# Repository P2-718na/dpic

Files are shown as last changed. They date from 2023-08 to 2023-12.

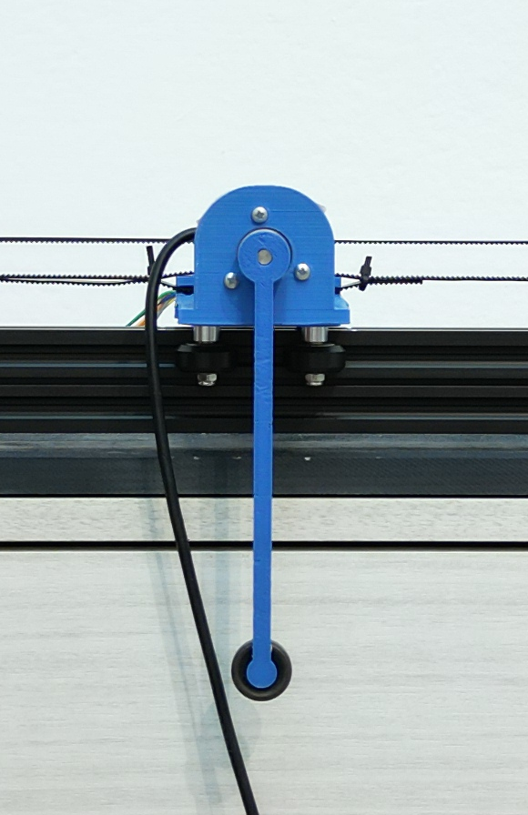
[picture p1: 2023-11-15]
docs/report/assets/dettaglio-carrello.png

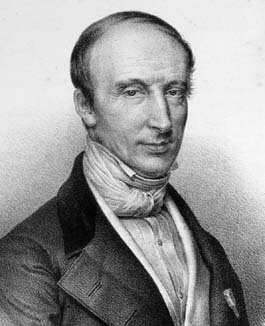
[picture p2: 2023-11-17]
docs/report/assets/cauchy.png

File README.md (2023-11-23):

# inverted-pendulum
tbd

## Repository structure
- 📁 [code](https://github.com/P2-718na/dpic/tree/master/code)
  - Code used for pendulum control and data acquisition.
- 📁 [docs](https://github.com/P2-718na/dpic/tree/master/docs)
  - Final report and other documentation.
- 📁 [scripts](https://github.com/P2-718na/dpic/tree/master/scripts)
  - npm scripts.

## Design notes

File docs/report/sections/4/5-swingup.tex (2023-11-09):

\section{Strategia di swing-up}
Per lo swing-up uso il metodo di Ljapunov.
%così come descritto in [Astrom Furuta swinging up a pendulum by energy control].
%todo ref
Ricavo l'energia del solo pendolo e la uso per cercare una funzione
di controllo di Ljapunov.

\subsection{Energia del pendolo}
\label{subsec:energia-pendolo}
L'energia del solo pendolo è data da
\begin{align*}
    E &= T + V\\
      &= \frac 1 2 I \dot \theta^2 + mgl(\cos\theta-1)
    \numberthis \label{eq:energia-pendolo}
\end{align*}
dove ho scelto il potenziale in modo che si annulli quando $\theta=0$. Voglio studiare che effetto ha un accelerazione del perno sul pendolo. Risolvo l'equazione di eulero:
\begin{equation*}
    \totald t \partiald {\dot \theta} {\mathcal L} - \partiald {\theta} {\mathcal L} = -lma \cos \theta
\end{equation*}
dove $\mathcal L$ è la Lagrangiana del solo pendolo e a secondo membro compare il momento torcente che l'accelerazione $a$ imprime al pendolo.
Ottengo
\begin{equation}
    I \ddot \theta - mgl\sin \theta + mal \cos \theta = 0
    \label{eq:moto-pendolo}
\end{equation}
%todo qui bisogna sistemare un po' i simboli
e posso usare le due equazioni \eqref{eq:moto-pendolo} e \eqref{eq:energia-pendolo} per calcolare la variazione di energia istantanea che produce l'accelerazione $a$ lungo la traiettoria del moto.
Ottengo
\begin{equation*}
    \begin{aligned}
        \frac{dE}{dt}
        &= \totald t \left(\frac 1 2 I \dot \theta ^2 + mgl \cos \theta  \right) \\
        &= I \dot \theta \ddot \theta - mgl \sin \theta \cdot \dot \theta \\
        &= -mal \cos \theta \cdot \dot \theta
        .
        \label{eq:effetto-energia}
    \end{aligned}
\end{equation*}

\subsection{Funzione di controllo di Ljapunov}
Cerco una funzione di controllo di Ljapunov.
Prendo
\begin{equation}
    V = V(\b x) = \frac 1 2 E^2
        \label{eq:lyapunov-energy}
\end{equation}
e cerco una strategia di controllo $a$ per cui
\begin{equation*}
    \frac{dV}{dt}(\b x) < 0 \text{ con } \b x \neq \b 0,
\end{equation*}
secondo la proposizione~\ref{prop:condizione-sufficiente-ljapunov}.
Calcolo la derivata
\begin{align*}
    \frac{dV}{dt} &= \totald t \left( \frac 1 2 \dot E^2\right) \\
    &=  E \dot E \\
    &=  E (-mal \dot \theta \cos \theta) \numberthis\label{eq:dvdt}.
\end{align*}
La scelta più semplice è definire $a$ come funzione a tratti:
\begin{equation*}
    a = \left\{
    \begin{aligned}
         &a_{\max}\sign{\dot \theta \cos \theta} &\text{ se } E < 0 \\
         -&a_{\max}\sign{\dot \theta \cos \theta} &\text{ se } E > 0 \\
         &0 &\text{ altrimenti}
    \end{aligned}
    \right.
\end{equation*}
con $a_{\max}$ l'accelerazione massima possibile per il sistema.
La figura~\ref{fig:energy-control} mostra che questa strategia porta il sistema a
zero.

\begin{figure}
    \centering
    \begin{subfigure}[b]{0.48\textwidth}
        \centering
        
        \caption{aaaaa}
    \end{subfigure}
    \hfill
    \begin{subfigure}[b]{0.48\textwidth}
        \centering
        
        \caption{bbbbb}
    \end{subfigure}
    \caption{Schema del sistema.} %todo
    \label{fig:energy-control}
\end{figure}

La funzione segno nella~\eqref{eq:bang-bang} la rende difficile da studiare
ed estremamente sensibile al rumore (la minima oscillazione costringe il motore
a passare istantaneamente da potenza zero a potenza massima).
Considero l'alternativa
\begin{equation}
    a = a_{\max} \tanh(E \dot \theta \cos \theta).
    \label{eq:control-strategy-tanh}
\end{equation}

Dimostro che la~\eqref{eq:lyapunov-energy} con $a$ definito come
nella~\eqref{eq:control-strategy-tanh} è una funzione di controllo di Ljapunov.

Uso la~\eqref{eq:dvdt}:
\begin{align*}
    \frac{dV}{dt} &=  E (-mal \dot \theta \cos \theta)\\
    &= -Eml \dot \theta \cos \theta \cdot a_{\max} \tanh(E \dot \theta \cos \theta). \numberthis\label{eq:a-ljapunov}
\end{align*}
ed è immediato verificare che la~\eqref{eq:a-ljapunov} è sempre negativa.
La~\eqref{eq:control-strategy-tanh} è rappresentata in figura~\ref{fig:energy-control-better}.

\begin{figure}[b]
    \centering
    \begin{subfigure}[b]{0.48\textwidth}
        \centering
        
        \caption{aaaaa}
    \end{subfigure}
    \hfill
    \begin{subfigure}[b]{0.48\textwidth}
        \centering
        
        \caption{bbbbb}
    \end{subfigure}
    \caption{Schema del sistema.} %todo
    \label{fig:energy-control-better}
\end{figure}

Concludo osservando che la strategia che ho mostrato in questo paragrafo
non tiene conto della posizione del carrello sulla rotaia.
È quindi necessario passare alla strategia di stabilizzazione
una volta che il pendolo ha raggiunto la verticale.

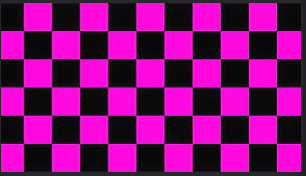
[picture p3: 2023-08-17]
docs/report/assets/missing.png

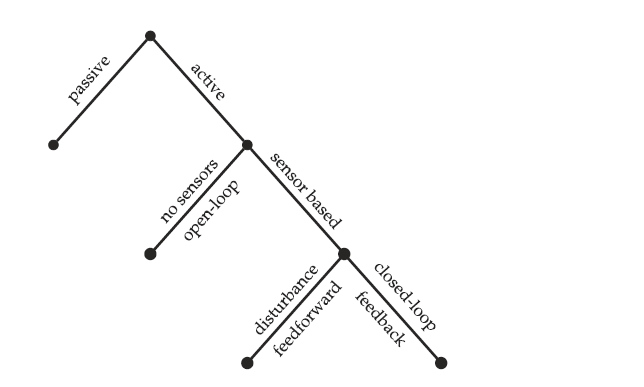
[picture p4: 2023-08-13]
docs/report/assets/control-types.png

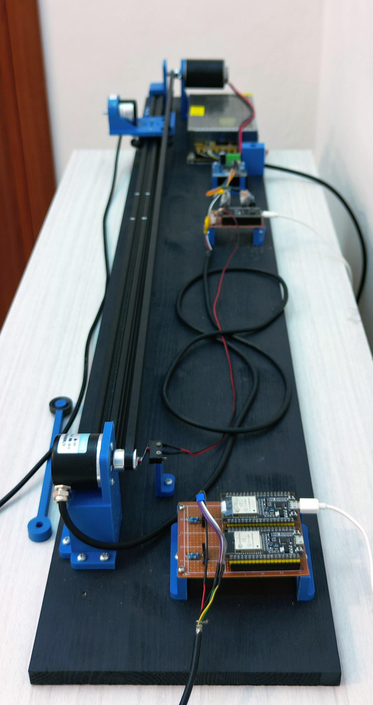
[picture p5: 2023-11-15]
docs/report/assets/lato.png

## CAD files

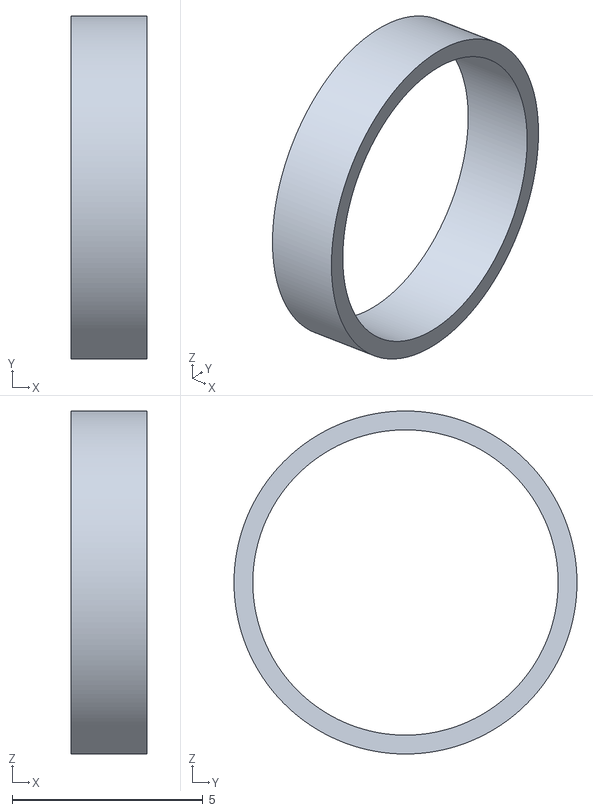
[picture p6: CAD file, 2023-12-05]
stl/spacer bearing.stl
2.00 x 8.99 x 8.99

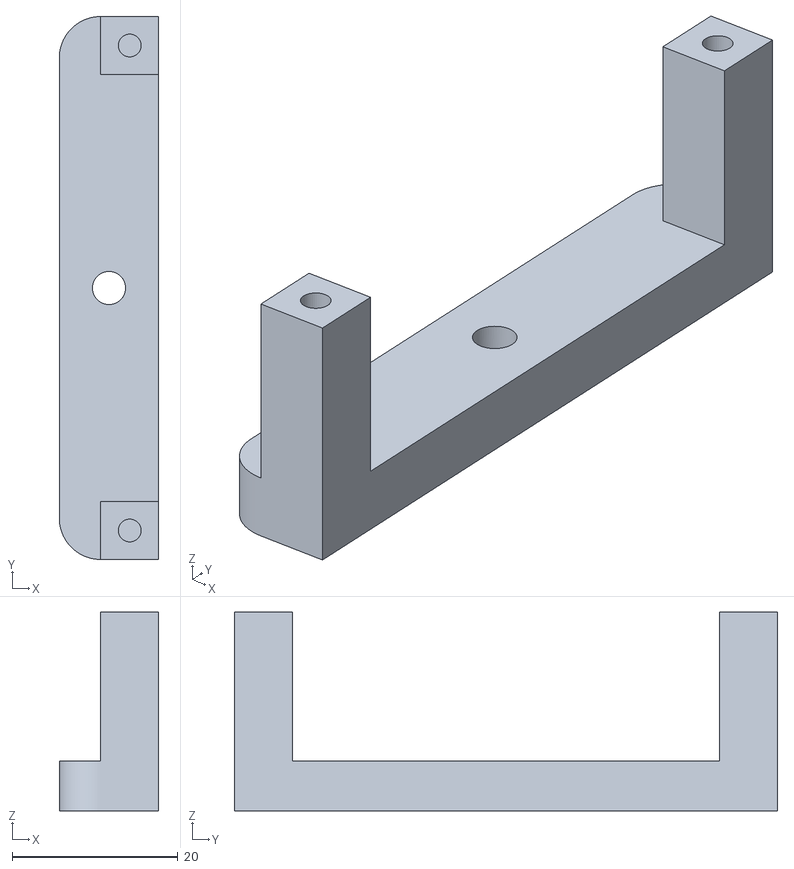
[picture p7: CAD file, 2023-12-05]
stl/raiser2.stl
12.0 x 65.5 x 24.0

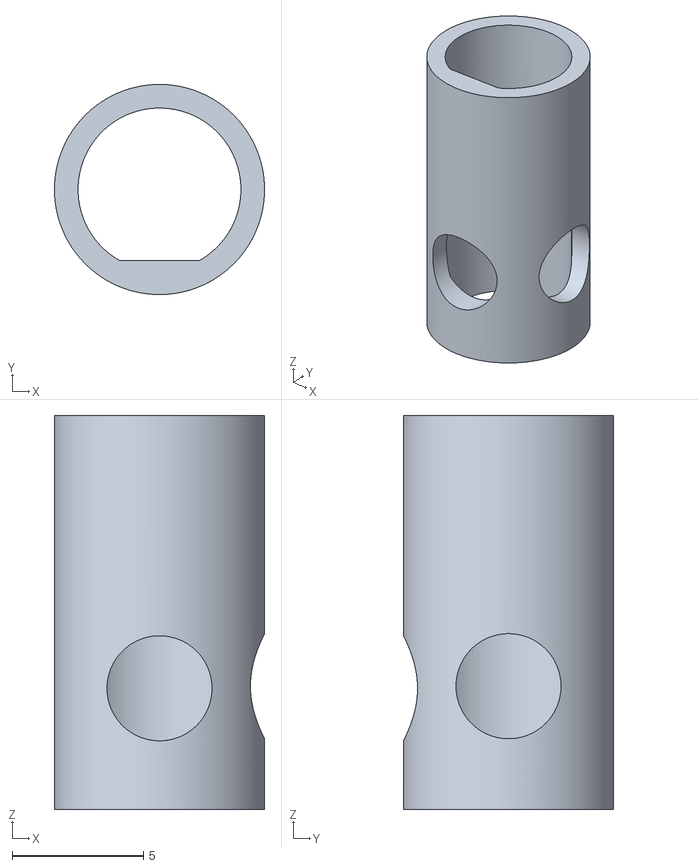
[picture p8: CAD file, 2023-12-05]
stl/Corpo67.stl
8.00 x 8.00 x 15.0

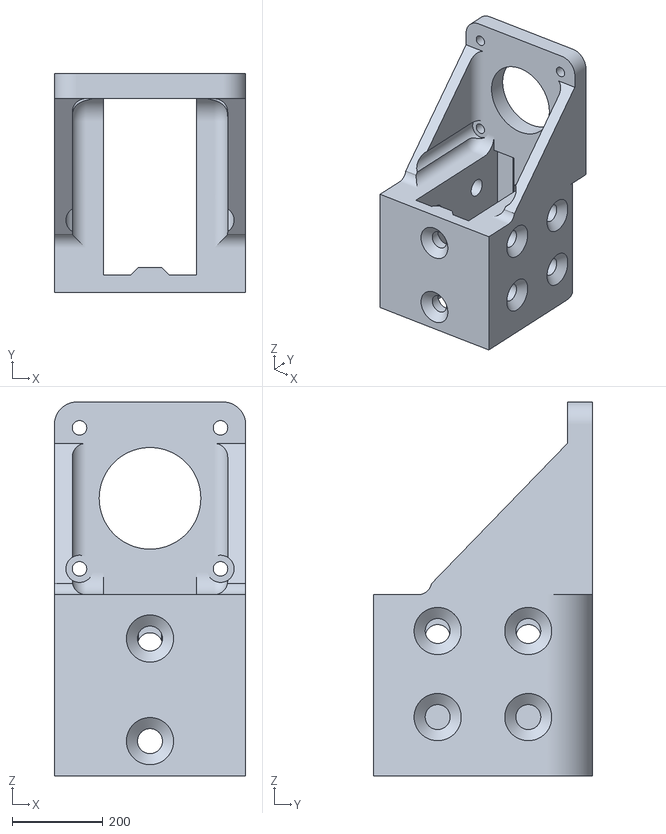
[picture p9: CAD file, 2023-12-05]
stl/holder.stl
422.2 x 482.4 x 825.0

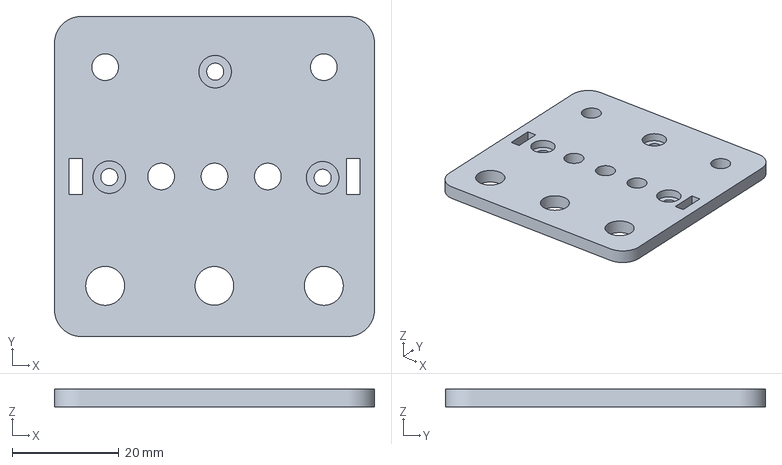
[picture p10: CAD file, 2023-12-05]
stl/GANTRY ADAPTER.3mf
60.0 x 60.0 x 3.35 mm

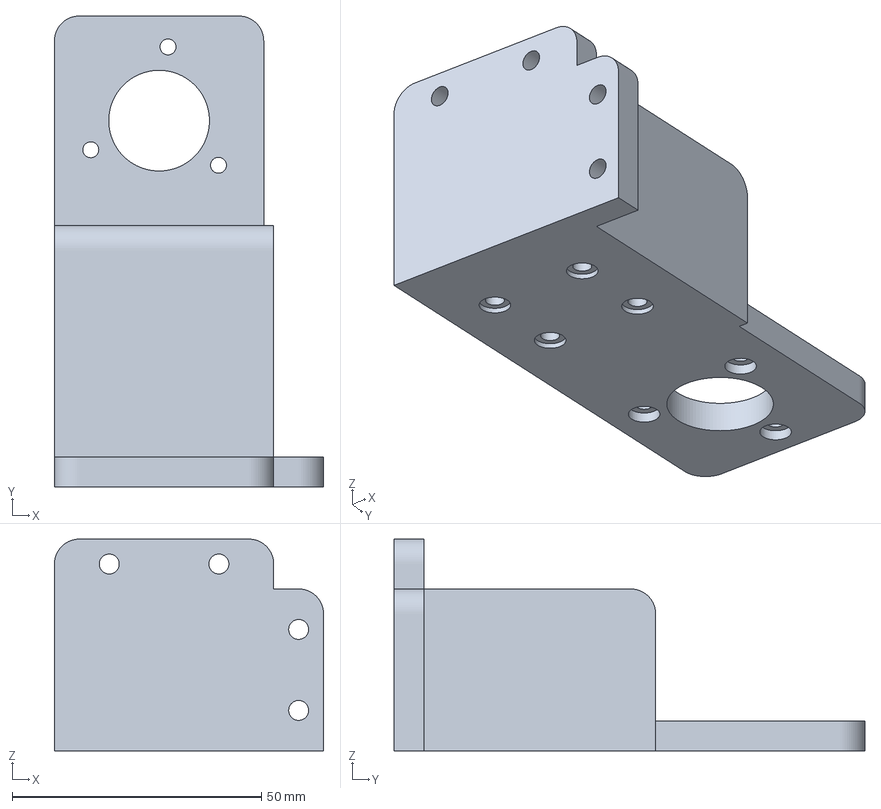
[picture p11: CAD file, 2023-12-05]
stl/stepper holder.3mf
54.0 x 94.5 x 42.5 mm

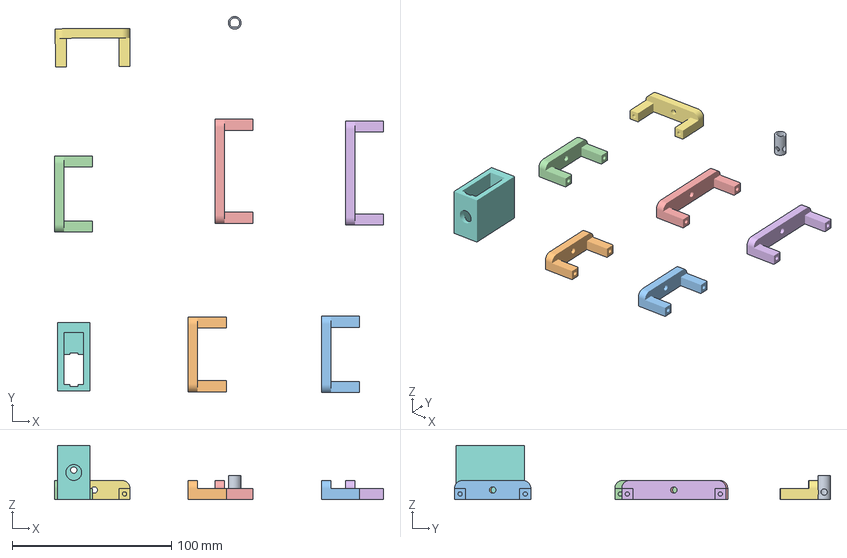
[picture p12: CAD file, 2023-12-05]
stl/last bits.3mf
207.2 x 236.4 x 34.0 mm
Corpo67.stl
raiser4.stl x 2
raiser3.stl x 2
raiser2.stl x 2
button.stl

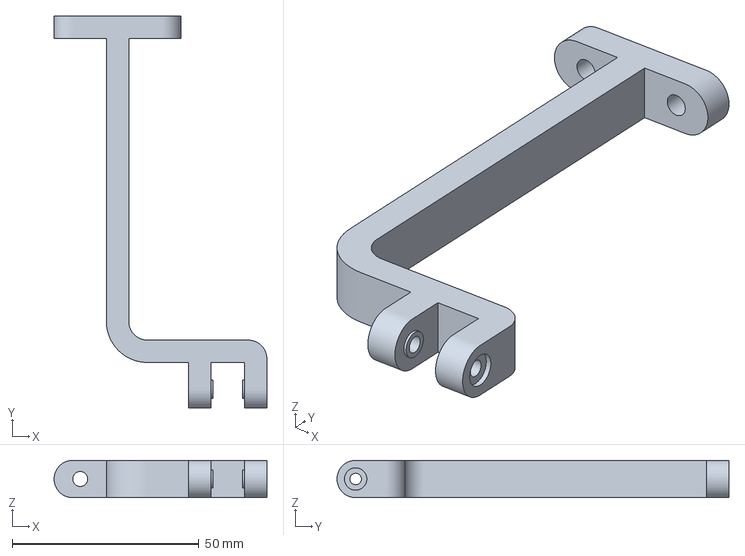
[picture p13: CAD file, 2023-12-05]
stl/tensioner.3mf
57.0 x 105.0 x 10.0 mm

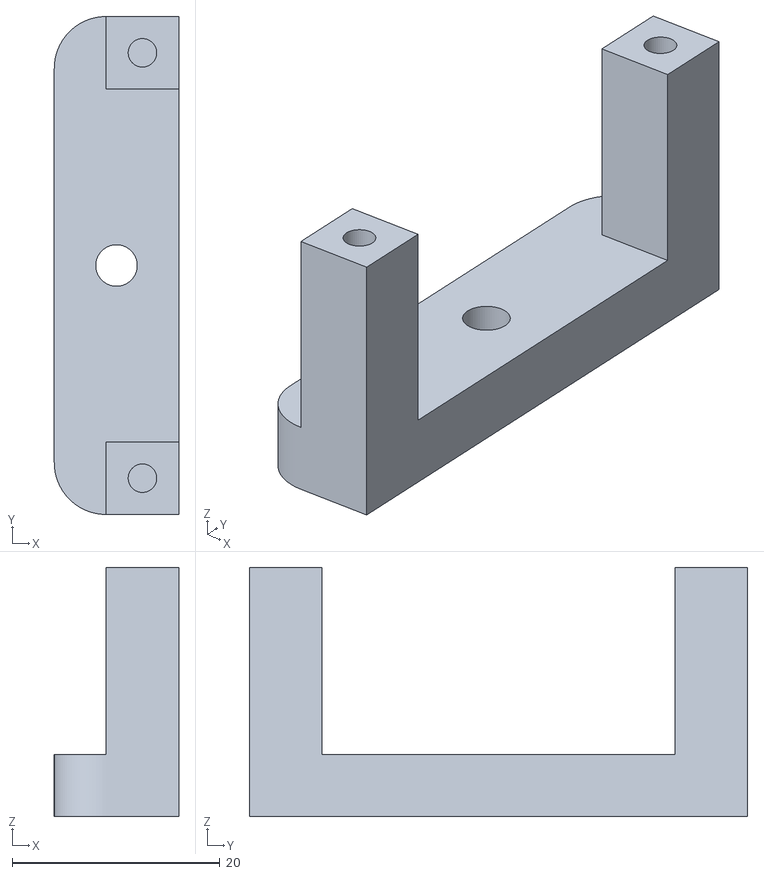
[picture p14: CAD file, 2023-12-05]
stl/raiser3.stl
12.0 x 48.0 x 24.0

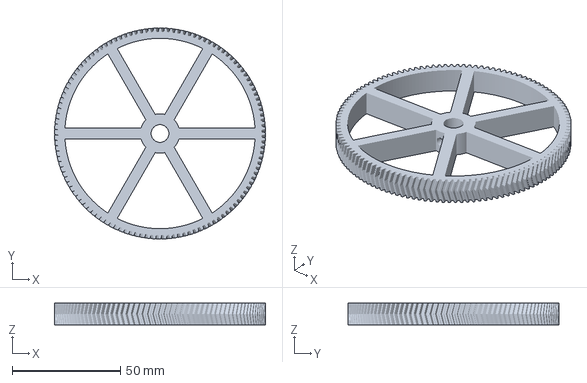
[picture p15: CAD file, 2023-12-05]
stl/gear.3mf
97.6 x 97.6 x 10.0 mm

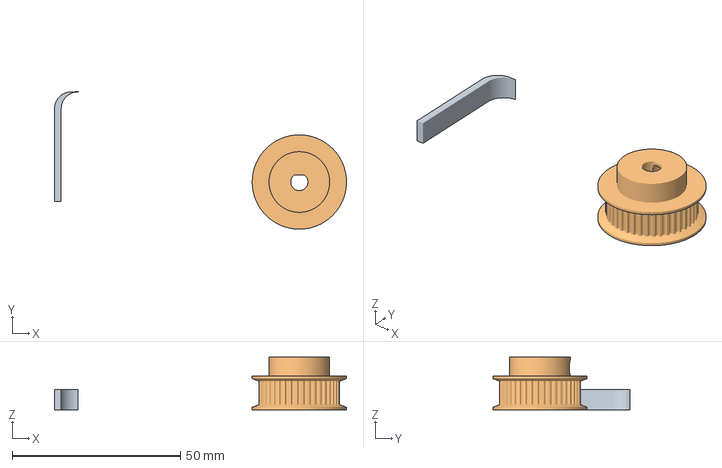
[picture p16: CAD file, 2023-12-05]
stl/pulley 40teeth.3mf
86.7 x 40.8 x 15.6 mm
Corpo148.stl
pulley 40teeth.stl

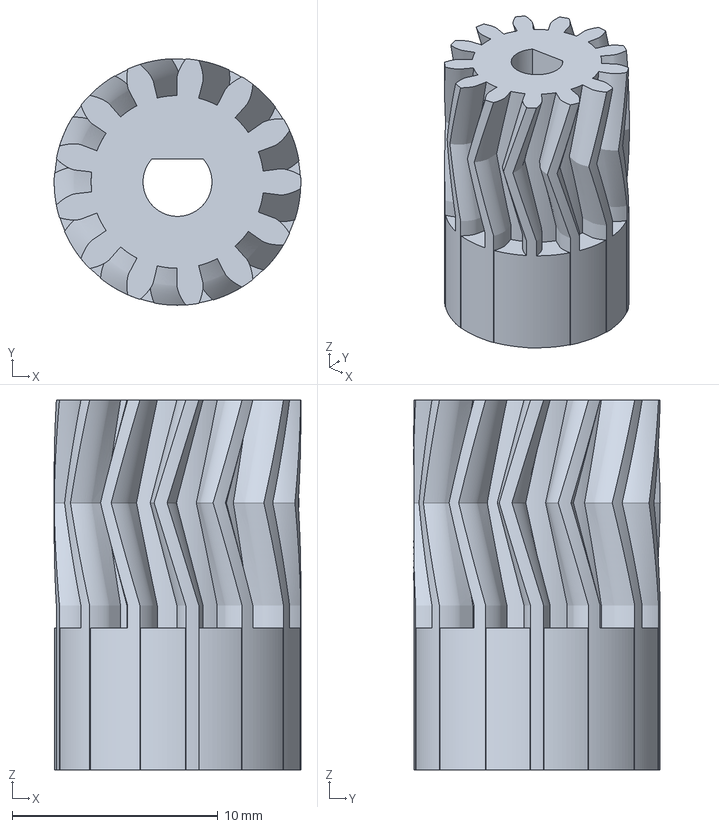
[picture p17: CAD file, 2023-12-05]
stl/gear small.3mf
12.0 x 12.0 x 18.0 mm

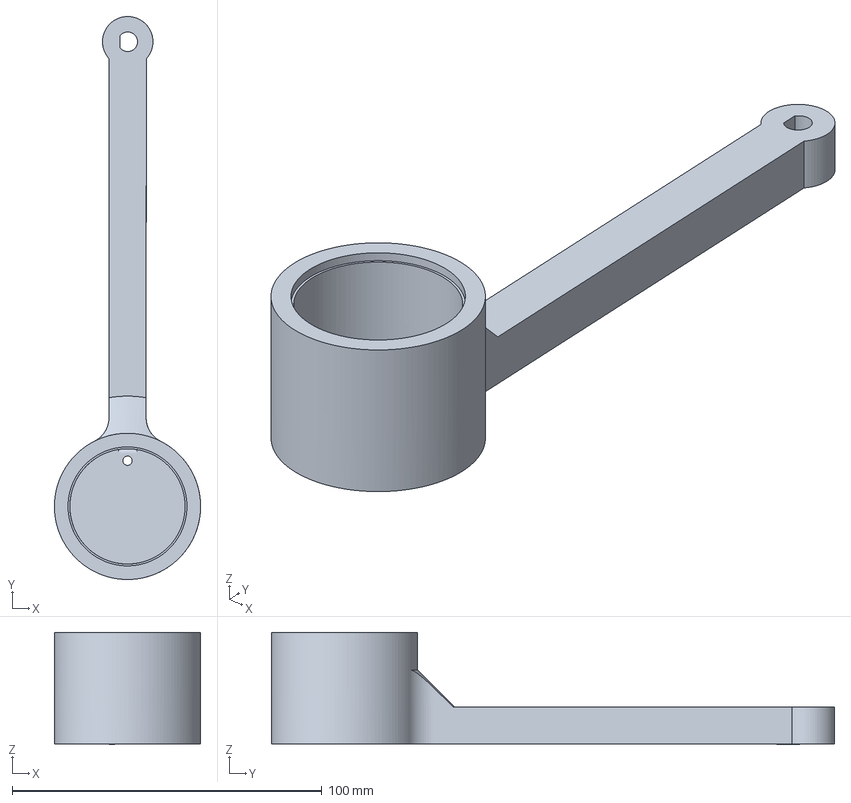
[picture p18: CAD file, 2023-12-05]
stl/Corpo1.3mf
47.2 x 181.7 x 36.2 mm

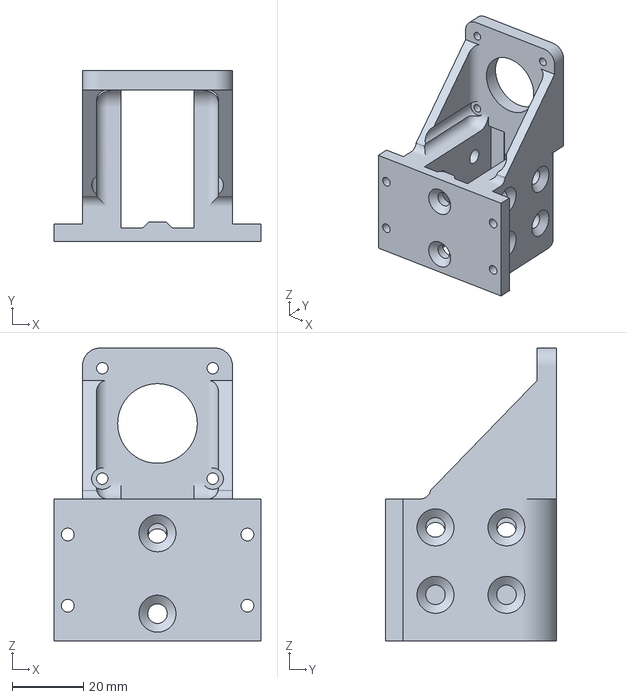
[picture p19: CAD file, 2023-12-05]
stl/Corpo della mesh1.3mf
58.2 x 48.2 x 82.5 mm

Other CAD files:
stl/rod2.3mf
stl/gears.3mf
stl/Corpo79.stl
stl/raiser4.stl
stl/Corpo1.stl
stl/Extrusion.f3d
stl/arm2.3mf
stl/button.stl
stl/encoder pulley.3mf
stl/lato Corpo1.3mf
stl/mover.f3d
stl/pulley 40teeth.stl
stl/stabilizer.stl
stl/tensioner.stl

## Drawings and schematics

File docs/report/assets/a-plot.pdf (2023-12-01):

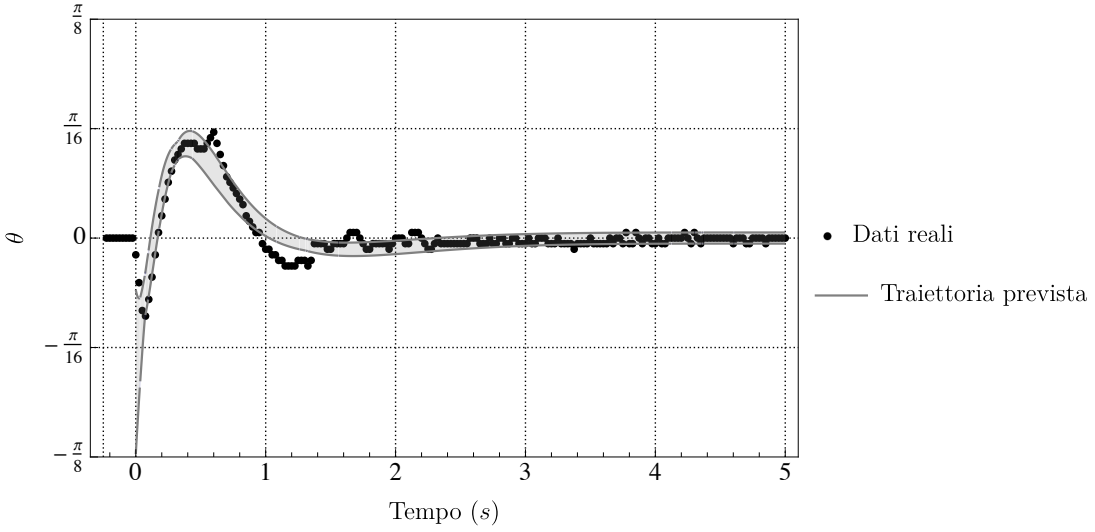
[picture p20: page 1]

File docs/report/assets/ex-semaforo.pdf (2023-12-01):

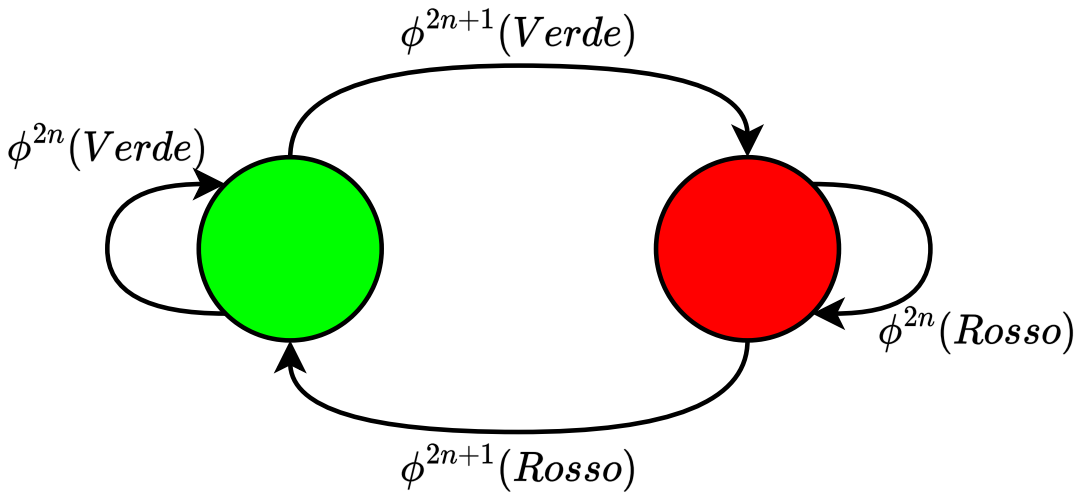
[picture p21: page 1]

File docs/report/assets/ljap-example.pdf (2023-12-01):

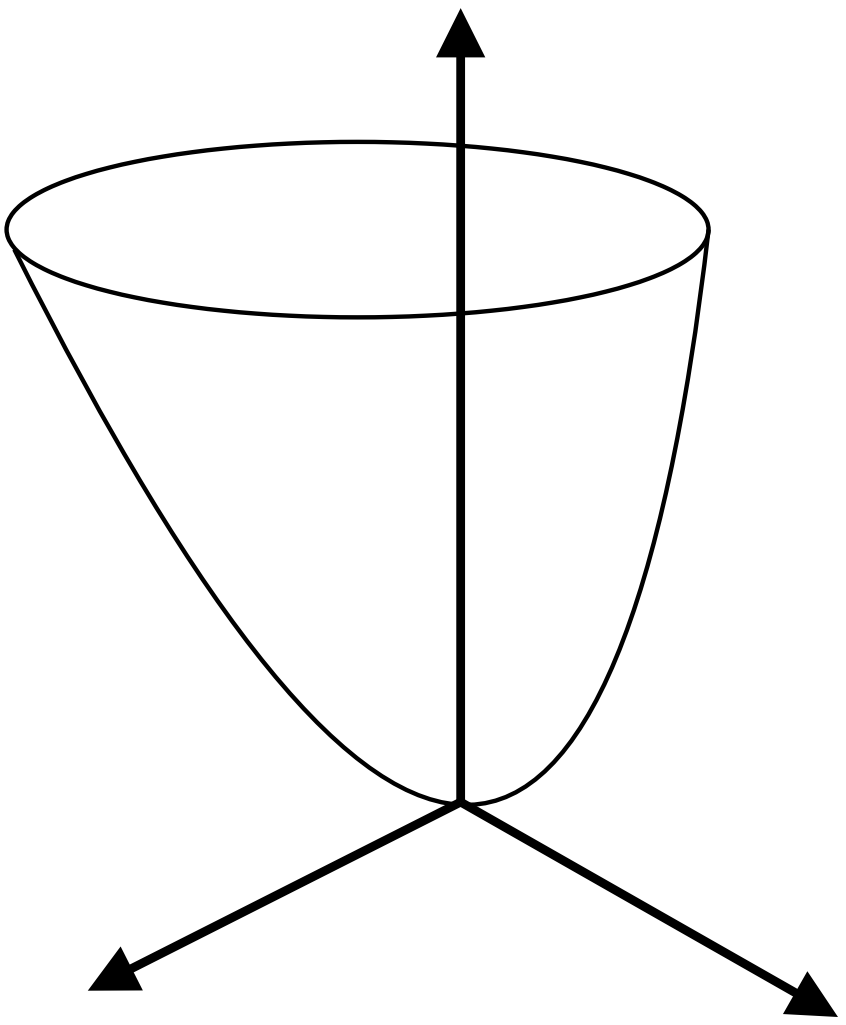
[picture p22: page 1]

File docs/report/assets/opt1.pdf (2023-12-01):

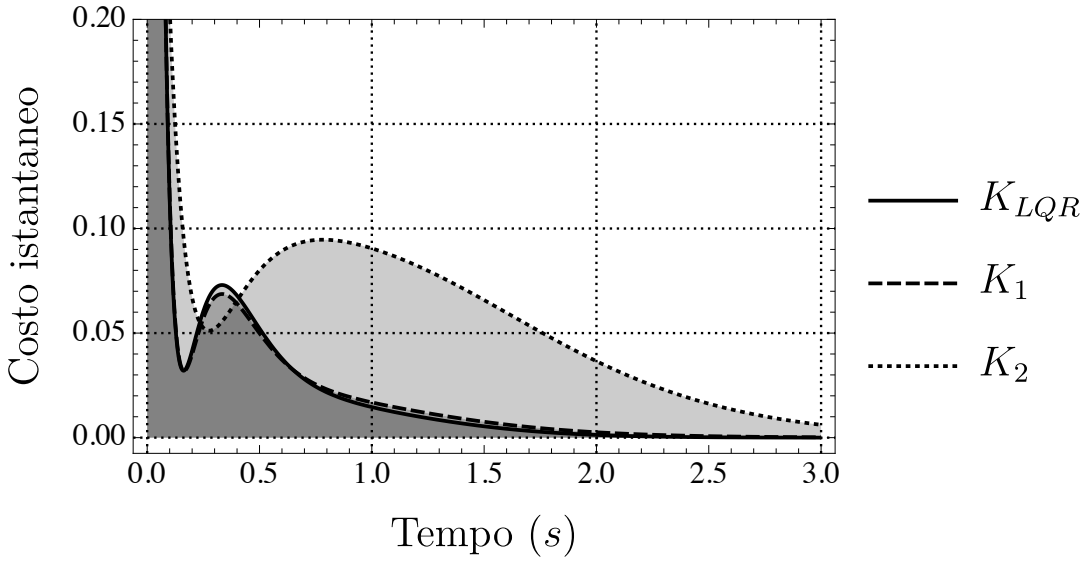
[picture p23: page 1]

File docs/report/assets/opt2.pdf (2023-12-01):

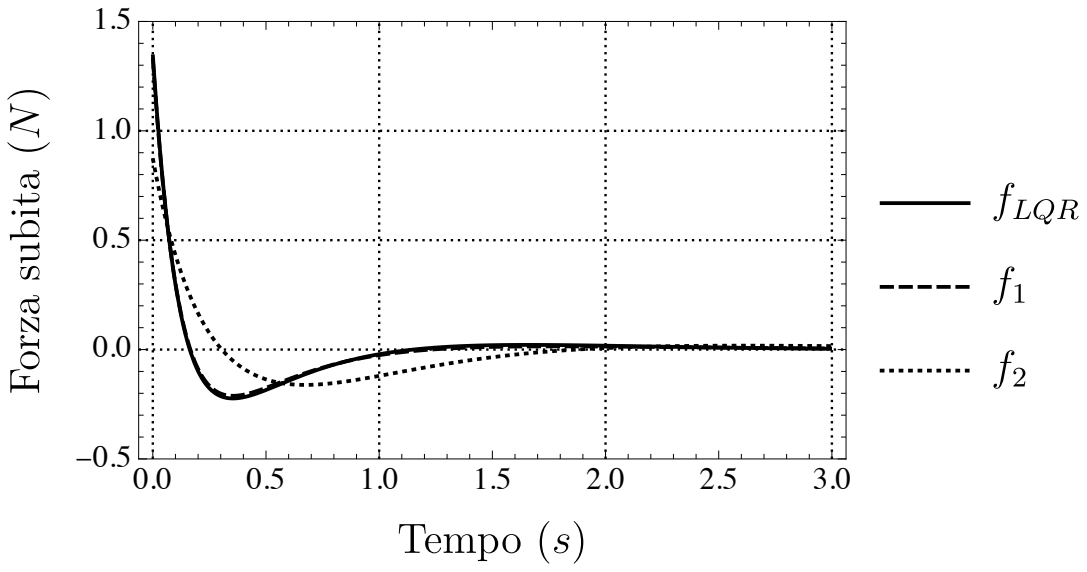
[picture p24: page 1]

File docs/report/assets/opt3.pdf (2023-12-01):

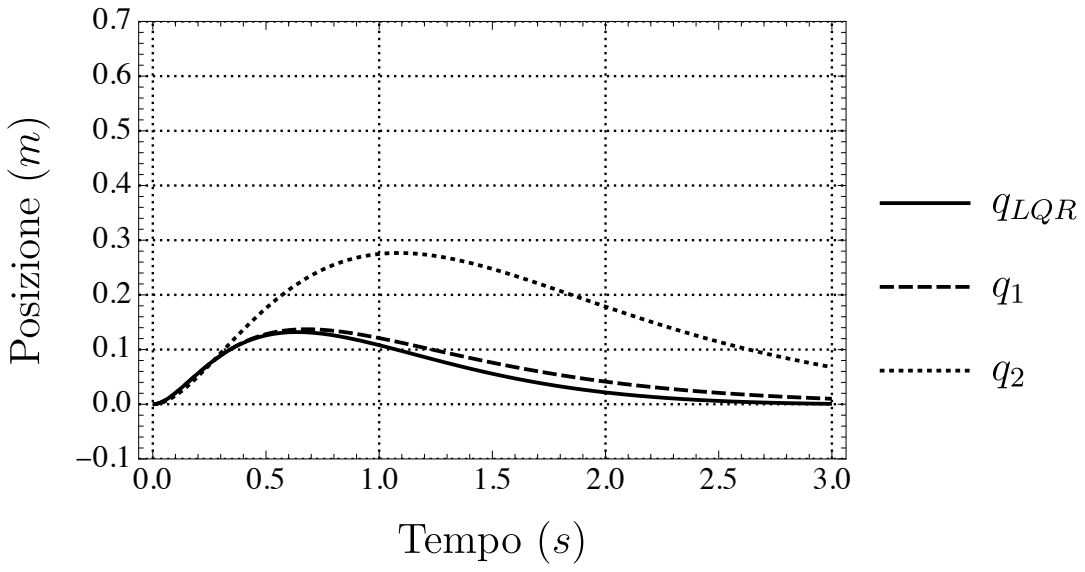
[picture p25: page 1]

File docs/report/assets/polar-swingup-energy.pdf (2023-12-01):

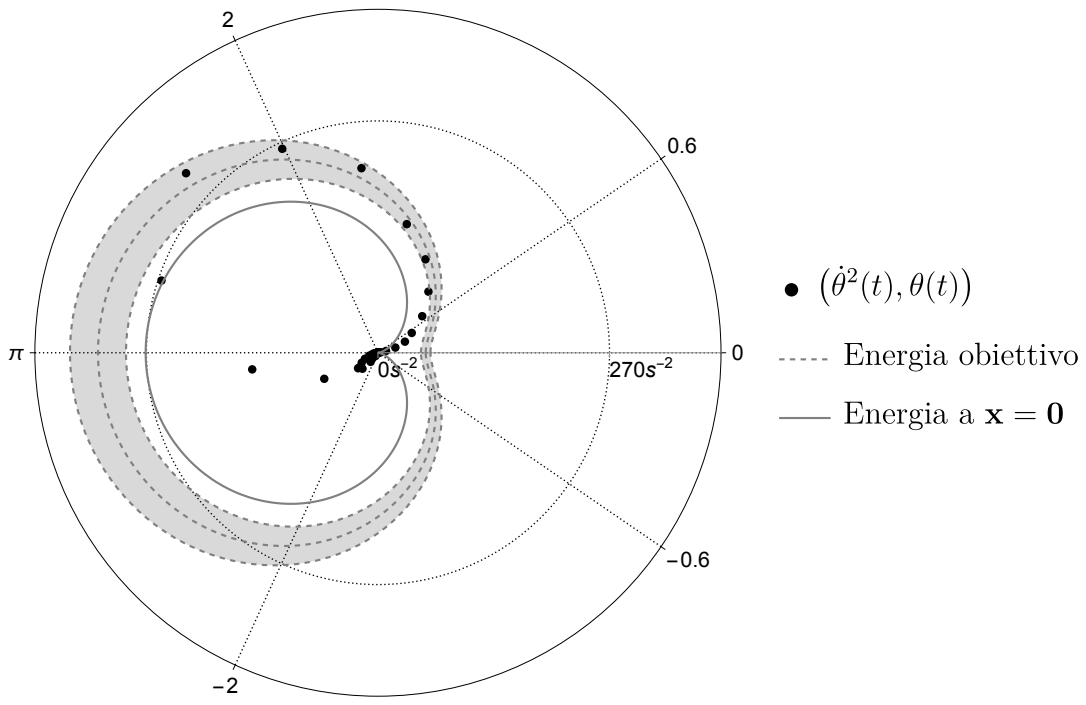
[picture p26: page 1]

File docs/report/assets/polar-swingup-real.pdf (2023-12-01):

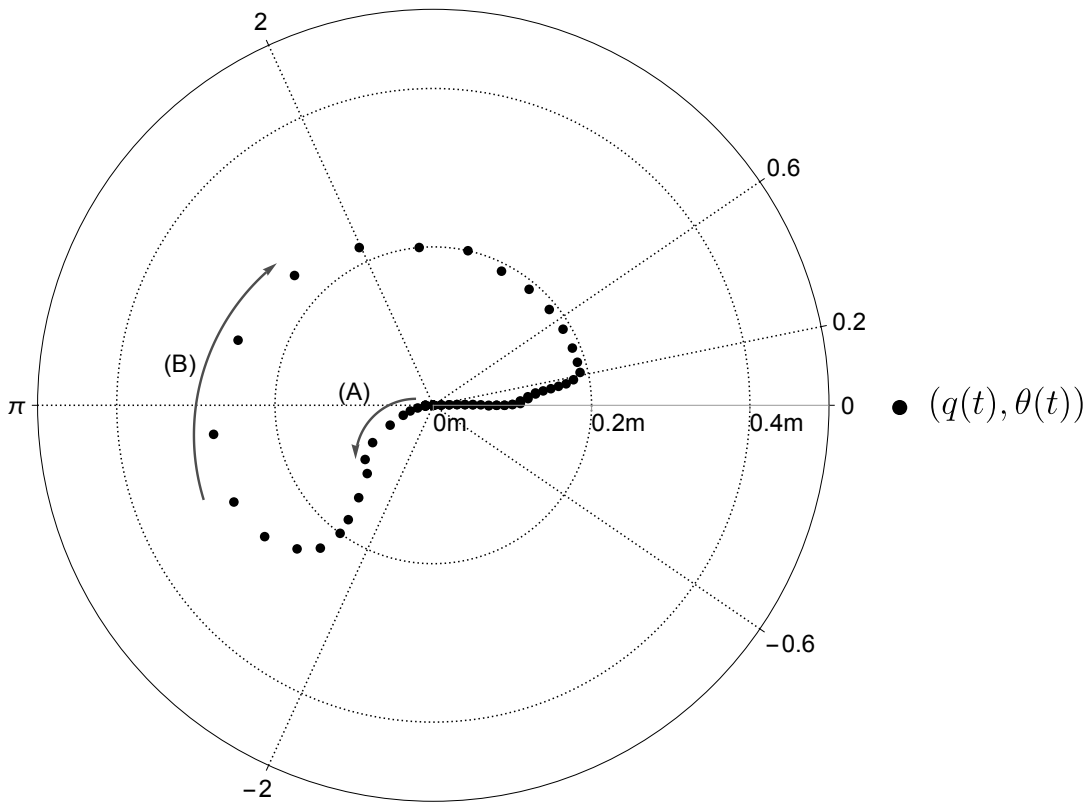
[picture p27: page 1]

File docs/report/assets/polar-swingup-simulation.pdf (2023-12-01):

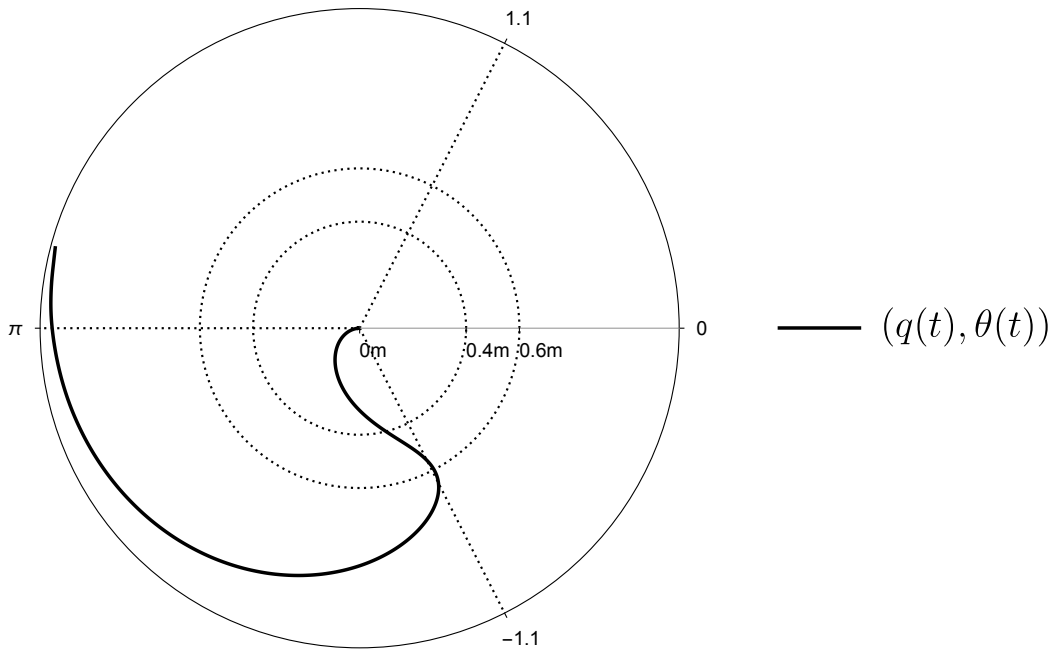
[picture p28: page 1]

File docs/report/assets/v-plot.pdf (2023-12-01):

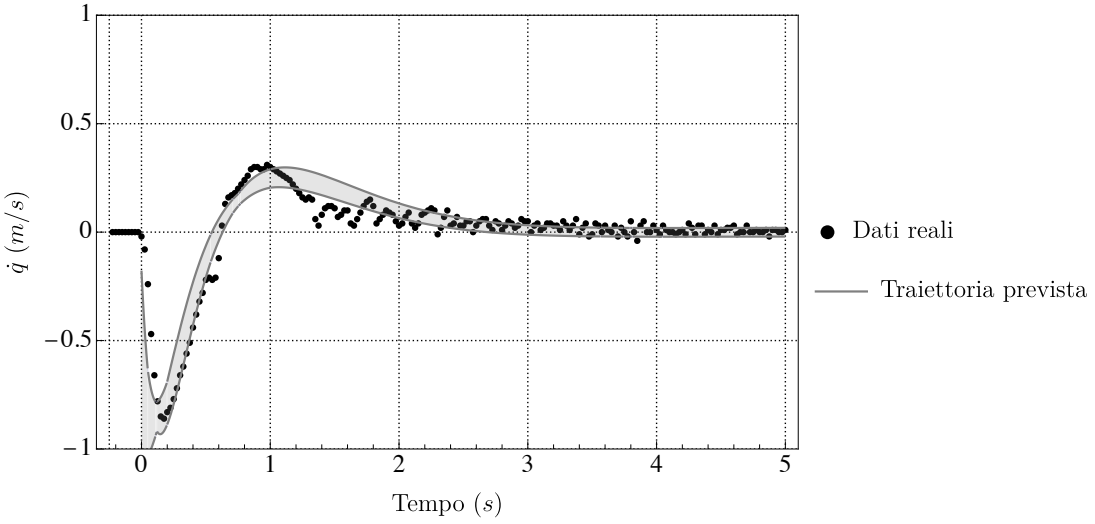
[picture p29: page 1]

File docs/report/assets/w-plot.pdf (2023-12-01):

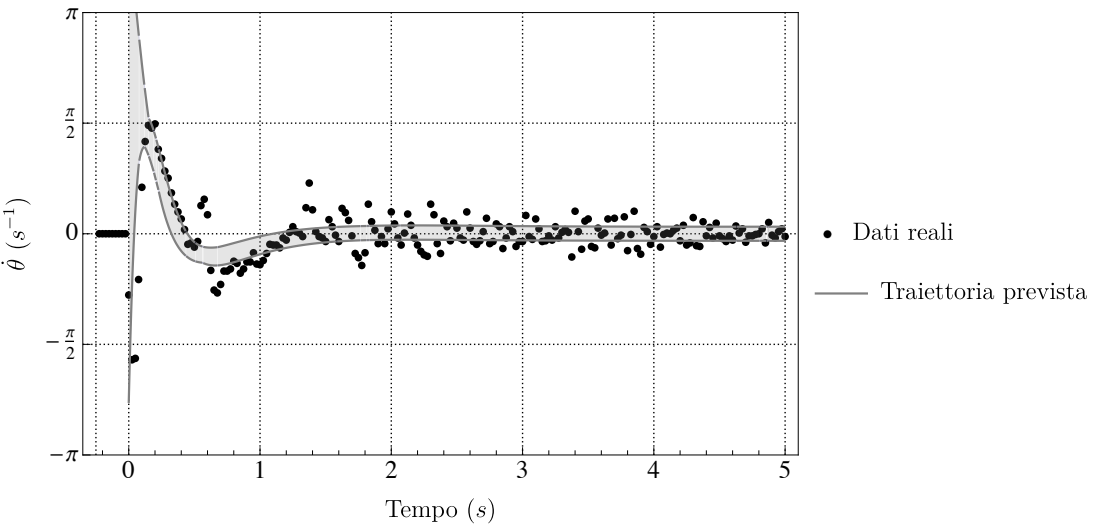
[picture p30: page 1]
πππ2

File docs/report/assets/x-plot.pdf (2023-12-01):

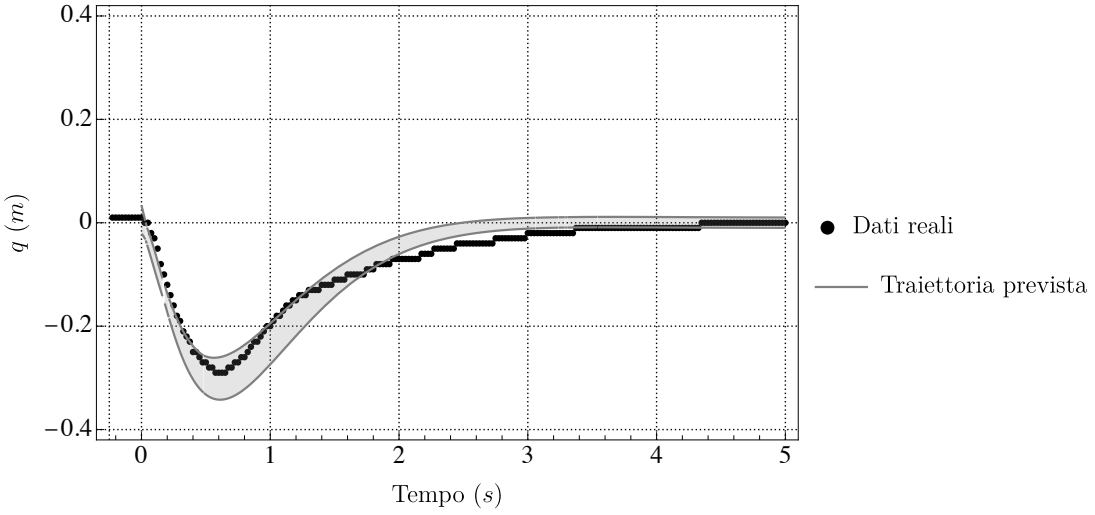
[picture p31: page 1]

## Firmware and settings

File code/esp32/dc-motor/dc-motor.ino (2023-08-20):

#include <esp_now.h>
#include <WiFi.h>
#include <Encoder.h>


// Constants 
#define RPWM_OUT 32
#define LPWM_OUT 33
#define RPWM_CHANNEL 0
#define LPWM_CHANNEL 1

#define ENCODER_A 35
#define ENCODER_B 34


// State  and control /////////////////////////////////////////////
struct State {
  float x, v, a1, w1, a2, w2;

  float optimalControl() {
    //return 2*cos(millis()/200.);
    return 1;
  }

  bool controllable() {
    return x < .7  && x > .01;
  }
};
State state;
void printState();


// Second core and x, v encoder ///////////////////////
volatile int steps;
void loop2(void * params) {
  Encoder encoder(ENCODER_A, ENCODER_B); //todo possibly edit code to add esp32 attribute needed for interrupts

  int lastStep = steps % 2400;
  for (;;) {
    steps = encoder.read();
  }
}

void setup2() {
  TaskHandle_t core2;

  xTaskCreatePinnedToCore(
      loop2, /* Function to implement the task */
      "DAQ", /* Name of the task */
      10000,  /* Stack size in words */
      NULL,  /* Task input parameter */
      0,  /* Priority of the task */
      &core2,  /* Task handle. */
      0); /* Core where the task should run */ //?? 
}



// First core //////////////////////////////////////////
void setup() {
  // Setup second core
  setup2();

  // Setup motor
  // channel, freq, resolution(bits)
  ledcSetup(RPWM_CHANNEL, 500, 8);
  ledcSetup(LPWM_CHANNEL, 500, 8);
  ledcAttachPin(RPWM_OUT, RPWM_CHANNEL);
  ledcAttachPin(LPWM_OUT, LPWM_CHANNEL);

  // Initialize communications
  Serial.begin(115200);
}

void loop() {

  // todo make better
  static int lastMicros;
  static int lastSteps;
  static int deltaTime;

  deltaTime = micros() - lastMicros;
  if (deltaTime > 5000) {
    constexpr float toMeters = .853 / 51144.;

    state.x = steps * toMeters;
    state.v = ((steps - lastSteps) * 1E6) / deltaTime * toMeters;
    lastMicros = micros();
    lastSteps = steps;
  }

  printState(state);

  applyControl(state);
}



// Function definitions /////////////////////////////////////
void printState(State& state) {
  static bool init = false;
  if (!init) {
    Serial.println("x v a1 w1 a2 w2");

    init = true;
  }

  static int interval = millis();
  if (millis() - interval < 100) {
    return;
  }

  Serial.print(state.x);
  Serial.print(" ");
  Serial.print(state.v);
  Serial.print(" ");
  Serial.println();

  interval = millis();
}

void applyControl(State& state) {
  static int interval = millis();
  if (millis() - interval < 20) {
    return;
  }


  float control = state.optimalControl();

  // QUi ci andrà uno switch per tutti i possibili stati del sistema (down, up, swing up...)
  if (state.controllable()) {
    //Serial.print("+");
    driveMotorWithForce(control, state.v);
    return;
  }

  //Serial.print("=");
  driveMotorWithForce(0, 0);
}

template <typename T> int sgn(T val) {
    return (T(0) < val) - (val < T(0));
}

// PEso motore: 225g senza filo, 240g con filo.
void driveMotorWithForce(float f, float v) {
    constexpr float A =  .656;
    constexpr float B =  .0616;
    constexpr float C = -.0535;

    // deltaT
    constexpr float dT = .02;

    //m
    constexpr float m = .8;

    float u = 
      ((1 - A)*v + dT*f/m - C*sgn(v))
      / 
      B;
    u = u *255./12.;

    if (f == 0) {
      ledcWrite(LPWM_CHANNEL, 0);
      ledcWrite(RPWM_CHANNEL, 0);

      return;
    }

    ledcWrite(LPWM_CHANNEL, (int)(u > 0 ?  u : 0));
    ledcWrite(RPWM_CHANNEL, (int)(u < 0 ? -u : 0));
}

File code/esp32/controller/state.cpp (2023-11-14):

#include "state.h"
#include "math.h"

State::State() : printInterval(Interval(25)), controlInterval(Interval(5)), currentControl(0) {}

void State::init() {
  Serial.println("x v a1 w1 a2 w2");
}

float State::optimalControl() {
 // return 1;
 // SIngle pendulum
  return (6.63*x + 6.77*v + 12.89*a1 + 1.5*w1);
  return -(1.8*x + 2.9*v - 30*a1 - 0.97*w1 + 80.5*a2 + 8.00*w2)*.1;
}

bool State::controllable() {
  //return x <.6 && x >.01;
  return (a1 > -.6  && a1 < .6 && x < .35 && x > -.35 && abs(w1) < 6 && abs(v) < 2);
  return (a1 > -.8  && a1 < .8 && x < .35 && x > -.35 && a2 > -.5  && a2 < .5);
}

void State::updateControl() {
  // Qui ci va lo switch in base allo stato del sistema...
  if (!controllable()) {
    currentControl = 0;

    constexpr float aMax = 18;
    const float E = .0243628 * (cos(a1) - 1) + .00018 * w1*w1;

    const float ctrl = aMax * tanh(
        (E -.010) * w1 * cos(a1)
    );

    if (abs(a1) > 2 && x < .3 && x > -.3) {
      currentControl = ctrl;
    }

    return;
  }

  //Serial.print(millis());
  //Serial.println("+");
  currentControl = optimalControl();
}

int State::convertToPWM(float force) {
  constexpr float A = 28.5;
  constexpr float B = 120 ; // Dovrebbe essere 8, ma 8 non va lol

  float u = A*force + B*v;

  return u;
}

void State::updateMotor() {
  if (currentControl == 0) {
    ledcWrite(LPWM_CHANNEL, 0);
    ledcWrite(RPWM_CHANNEL, 0);

    return;
  }

  int u = convertToPWM(currentControl);

  constexpr int LPWM_MIN = 33; //32 safe
  constexpr int RPWM_MIN = 33; // 32 safe

  ledcWrite(LPWM_CHANNEL, (int)(u > 0 ?  (u < LPWM_MIN ? u + LPWM_MIN : u): 0));
  ledcWrite(RPWM_CHANNEL, (int)(u < 0 ?  (-u < RPWM_MIN ? -u + RPWM_MIN : -u) : 0));
}

void State::print() {
  Serial.print("( ");
  Serial.print(x*10);
  Serial.print(", ");
  Serial.print(v*10);
  Serial.print(", ");
  Serial.print(a1*10);
  Serial.print(", ");
  Serial.print(w1*10);
  Serial.print(", ");
  Serial.print(a2);
  Serial.print(", ");
  Serial.print(w2);
  Serial.print(", ");
  Serial.print(optimalControl());
  Serial.print(", ");
  Serial.print(convertToPWM(optimalControl()));
  Serial.print(", ");
  Serial.print((int)controllable());
  Serial.print(" )");
  Serial.println();
}

void State::loop() {
  if (printInterval.ready()) {
    print();
    printInterval.reset();
  }

  updateMotor();

  if (controlInterval.ready()) {
    updateControl();
    controlInterval.reset();
  }
}

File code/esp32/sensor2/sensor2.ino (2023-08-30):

#include <esp_now.h>
#include <WiFi.h>
#include <Encoder.h>
#include <Ewma.h>
//EwmaT <int> speedFilter(33, 100);

#define ENCODER_A 35
#define ENCODER_B 34
#define BROADCAST_ADDRESS {0xBC, 0xDD, 0xC2, 0xD4, 0x52, 0x28}

struct Variable {
  byte id;
  float q;
  float q_dot;
};
Variable data;
uint8_t broadcastAddress[] = BROADCAST_ADDRESS;
void setupEspNow();



volatile int steps;
int euclideanMod(int a, int b);
void loop2(void * params) {
  Encoder encoder(ENCODER_A, ENCODER_B); //todo possibly edit code to add esp32 attribute needed for interrupts

  for (;;) {
    // maybe I cann add some sort of timer here...
    steps = encoder.read();
  }
}

void setup2() {
  TaskHandle_t core2;

  xTaskCreatePinnedToCore(
      loop2, /* Function to implement the task */
      "DAQ", /* Name of the task */
      10000,  /* Stack size in words */
      NULL,  /* Task input parameter */
      0,  /* Priority of the task */
      &core2,  /* Task handle. */
      0); /* Core where the task should run */ //??
}



void setup() {
  // Setup second core
  setup2();
  // For some reason, initializing serial here and not writing to console breaks esp now... ?
  //Serial.begin(115200);

  setupEspNow();
}

void loop() {
  static int lastMicros = 0;
  static int deltaTime;
  static int lastSteps;
  deltaTime = micros() - lastMicros;

  //if (deltaTime1 > 1001) {
  //  speedFilter.filter((steps - lastSteps) * 1E6 / deltaTime1);
  //  lastSteps = steps;
  //  lastMicros1 = micros();
  //}

  // 5ms delay between sends
  if (deltaTime > 2000) {
    constexpr float toRadians = M_PI / 1200.;

    // Just to be sure, I want to avoid race conditions.
    const int currentSteps = steps;

    static Ewma q_dotFilter(.1);

    data.id     = 2;
    data.q      = (float)(euclideanMod(currentSteps + 1200, 2400) - 1200) * toRadians ;
    data.q_dot  = q_dotFilter.filter(
        (float)(currentSteps - lastSteps) / (float)deltaTime * toRadians * 1E6
    );

    // Send message via ESP-NOW
    esp_err_t result = esp_now_send(broadcastAddress, (uint8_t *) &data, sizeof(data));

    lastSteps = currentSteps;
    lastMicros = micros();
  }
}



void setupEspNow() {
  // Master esp32
  esp_now_peer_info_t peerInfo;

  // Set device as a Wi-Fi Station
  WiFi.mode(WIFI_STA);
  WiFi.disconnect();

  // Init ESP-NOW
  if (esp_now_init() != ESP_OK) {
    Serial.println("Error initializing ESP-NOW");
    return;
  }

  // Register peer
  memcpy(peerInfo.peer_addr, broadcastAddress, 6);
  peerInfo.channel = 0;
  peerInfo.encrypt = false;

  // Add peer        
  if (esp_now_add_peer(&peerInfo) != ESP_OK){
    Serial.println("Failed to add peer");
    return;
  }
}

int euclideanMod(int a, int b) {
  int mod = a % b;
  return mod > 0 ? mod : mod + b;
}

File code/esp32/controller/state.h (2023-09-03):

#ifndef STATE_H
#define STATE_H
#include <Arduino.h>
#include "interval.h"

// Constants
#define RPWM_OUT 33
#define LPWM_OUT 32
#define RPWM_CHANNEL 0
#define LPWM_CHANNEL 1



template <typename T> inline int sgn(T val) {
  return (T(0) < val) - (val < T(0));
}

struct State {
  float x, v, a1, w1, a2, w2;
  float currentControl;
  Interval printInterval;
  Interval controlInterval;

  State();
  void init();
  float optimalControl();
  bool  controllable();
  void  updateControl();
  void  updateMotor();
  int   convertToPWM(float control);
  void  print();
  void  loop();
};

#endif

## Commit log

2023-08-06 Add arduino IDE code
2023-08-10 Add Calibration
2023-08-11 Add full calibration data
2023-08-18 Update sensor 1 code
2023-08-20 Works with encoder
2023-09-03 Update coefficients and motor pins
2023-09-22 Velocity based swing up
2023-11-12 Add graphs
    [-10.csv, -11.csv, -4.csv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]
2023-11-12 B4 new calibration
2023-11-13 Add data
    [-10.csv, -11.csv, -3.csv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]
2023-11-13 6.1, 6.2
    [.8.csv, .9.csv, 1.csv]
2023-11-13 Grafici della vita
    [run.csv]
2023-11-14 Add last plots
    [swingup-fast-multi.csv]
2023-11-14 Add datasets
    [Foglio excel con i grafici.xlsx]
2023-11-26 fixes before new print
2023-11-26 fixes before new print2
2023-12-05 Add stl
    [Corpo della mesh1.3mf, Corpo1.3mf, Corpo1.stl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]
